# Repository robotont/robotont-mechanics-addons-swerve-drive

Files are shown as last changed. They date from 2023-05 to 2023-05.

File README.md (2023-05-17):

# Design and production files
Here are production and design files for the modular swerve drive add-on for Robotont.

The files are broken down based on file type as follows:
- step: 3D models as generally used step format;
- stl: 3D models formated for 3D printing;
- 3mf: Prusa Slicer project files containing models for 3D printing;
- gcode: files which contain gcode commands for Prusa 3D printer. (Some of the .gcode files are compressed as .zip due to github file size limitations)
- sldasm and sldprt: files containing the original 3D models designed in Solidworks.

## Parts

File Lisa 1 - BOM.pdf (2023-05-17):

## Lisa 1 – Materjalide nimekiri ühe mooduli kohta

Nr | Komponendi kirjeldus | Failinimi | Kogus | Tellimisviit | Kas prinditav/ tellitav/ freesitav
1 | Pololu 19:1 mootor 37Dx68L mm 12V koos 64 CPR kodeerijaga | BDSG-37-40-R150_motor [38] | 2 | https://www.pololu.com/product/4751/spe cs (https://www.pololu.com/product/4751/specs) | tellitav
2 | Rulluisuratas

70x25mm

scooter_wheel_7

0mm

1 | https://www.pololu.c

om/product/3272 (https://www.pololu.com/product/3272)

kasutatud

prototüübis:

https://kaup24.ee/et/s

port-puhkus-

turism/jalgrattad-

rulluisud-

rulad/rulluisud/rullui

surattad-nils-

extreme-70x24-mm-

82a-

mustad?id=5890108

&mid=7538983&ut

m_campaign=17169

_EE&utm_content=c

art_block&utm_med

ium=email&utm_so

urce=transactional&

utm_subscriber=119

580977 (https://kaup24.ee/et/sport-puhkus-turism/jalgrattad-rulluisud-rulad/rulluisud/rulluisurattad-nils-extreme-70x24-mm-82a-mustad?id=5890108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)

tellitav

3 | Ratta kinnitus võllile (võlli diameeter 6mm) | wheel_mount_h ub2 | 1 | https://www.pololu.com/product/2674 (https://www.pololu.com/product/2674) (komplekt) | tellitav/ prinditav
4 | Ratta kinnituse vastus | wheel_mount_h ub1 | 1 | | tellitav/ prinditav
5 | ratta võll l=59.1mm tihke istuga | shaft_round_wc ut_6mm_for_wh eel | 1 | https://www.alas-kuul.ee/lineaarjuhik-karastatud-ja-lihvitud-59-hrc-iso-h6-ots-markeeritud-rohelise-varviga-ljm-6-mad-1000-mm (https://www.alas-kuul.ee/lineaarjuhik-karastatud-ja-lihvitud-59-hrc-iso-h6-ots-markeeritud-rohelise-varviga-ljm-6-mad-1000-mm) | tellitav
6 | vedava mootori ülekande võll l=16.7mm tihke istuga | shaft_round_wc ut_6mm_for_mo tor_transmission 1 | 1 | https://www.alas-kuul.ee/lineaarjuhik-karastatud-ja-lihvitud-59-hrc-iso-h6-ots-markeeritud-rohelise-varviga-ljm-6-mad-1000-mm (https://www.alas-kuul.ee/lineaarjuhik-karastatud-ja-lihvitud-59-hrc-iso-h6-ots-markeeritud-rohelise-varviga-ljm-6-mad-1000-mm) | tellitav
7 | keskmiste hammasrataste ülekande võll l=45.1mm | shaft_round_wc ut_6mm_for_mi dgears | 1 | https://www.alas-kuul.ee/lineaarjuhik-karastatud-ja-lihvitud-59-hrc-iso-h6-ots-markeeritud-rohelise-varviga-ljm-6-mad-1000-mm (https://www.alas-kuul.ee/lineaarjuhik-karastatud-ja-lihvitud-59-hrc-iso-h6-ots-markeeritud-rohelise-varviga-ljm-6-mad-1000-mm) | tellitav
8 | võll ratta kõrvale koonushammasrat aste ülekandele l=49.5mm tihke istuga | shaft_round_wc ut_6mm_for_be vel_wheel_trans mission | 1 | https://www.alas-kuul.ee/lineaarjuhik-karastatud-ja-lihvitud-59-hrc-iso-h6-ots-markeeritud- (https://www.alas-kuul.ee/lineaarjuhik-karastatud-ja-lihvitud-59-hrc-iso-h6-ots-markeeritud-rohelise-varviga-ljm-6-mad-1000-mm) | tellitav

| | | | rohelise-varviga-ljm-6-mad-1000-mm (https://www.alas-kuul.ee/lineaarjuhik-karastatud-ja-lihvitud-59-hrc-iso-h6-ots-markeeritud-rohelise-varviga-ljm-6-mad-1000-mm)
9 | Koonushammasra tas ratta ülekandele väline 1.5M 16GT | bevel_gear_1.5 M_16GT_35570 700 | 1 | https://www.maedler.de/Article/35570700 (https://www.maedler.de/Article/35570700) | tellitav/ prinditav
10 | Koonushammasra tas ratta ülekandele sisemine 1.5M 16GT | bevel_gear_1.5 M_16GT_35570 700_inner | 1 | https://www.maedler.de/Article/35570700 (https://www.maedler.de/Article/35570700) | tellitav/ prinditav
11 | Silinderhammasra tas 72T 1M alumine | spur_gear_lower _1M_72T_2830 7201 | 1 | https://www.maedler.de/Article/28307201 (https://www.maedler.de/Article/28307201) | tellitav/ prinditav
12 | Silinderhammasra tas 72 1M ülemine | spur_gear_upper _1M_72T_2830 7201 | 1 | https://www.maedler.de/Article/28307201 (https://www.maedler.de/Article/28307201) | tellitav/ prinditav
13 | 72T-de vaheline hammasratas 26T 1M | spur_gear_long_ hub_26T_28302 601 | 1 | https://www.maedler.de/Article/28302601 (https://www.maedler.de/Article/28302601) | tellitav/ prinditav
14 | 72T-de vaheline hammasratas 26 T 1M, topelt keskmikuga, koonushammasrat ta võllil | spur_gear_26T_ mid_double_hub _28302601 | 1 | https://www.maedler.de/Article/28302601 (https://www.maedler.de/Article/28302601) | tellitav/ prinditav
15 | Koonushammasra tas 1M 16GT pöörava mootori (1.) nurkülekanne | small_bevel_gea r_1M_16GT_35 550701 | 1 | https://www.maedler.de/Article/35550701 (https://www.maedler.de/Article/35550701) | tellitav/ prinditav

16 | Koonushammasra tas 1M 16GT pöörava mootori nurkülekanne, lühem | small_bevel_gea r_CUT_1M_16 GT_35550701 | 1 | https://www.maedler.de/Article/35550701 (https://www.maedler.de/Article/35550701) | tellitav/ prinditav
17 | 26T 1M hammasratta väline ülekanne 1. mootori (pöörav) jaoks | spur_gear_CUT _26T_28302601 | 1 | https://www.maedler.de/Article/28302601 (https://www.maedler.de/Article/28302601) | tellitav/ prinditav
18 | Komponendi 16 ja 17 ühendatud versioon (alternatiivne printimiseks) | small_bevel_gea r1M_merged_wi th_spur_gear26 T_28302601_35 550701 | 1 | - | prinditav
19 | Silinderhammasra tas 24T 1M vedava mootori ülekanne | spur_gear_secon d_motor_transm ission_1M_24T _28302401 | 1 | https://www.maedler.de/Article/28302401 (https://www.maedler.de/Article/28302401) | tellitav/ prinditav
20 | Rulluisurattale 70mm kuullaager sisemine D=6mm, väline D=19mm, W=6mm | ball_bearing_SK F626 | 2 | https://tellimiskeskus.moduator.ee/index.php?pg=1&tg=155&kg=30&aid=52789 (https://tellimiskeskus.moduator.ee/index.php?pg=1&tg=155&kg=30&aid=52789) | tellitav
21 | Nõellaager sisemine D=6mm, väline 10mm, W=8mm | needle_roller_be aring 6-10-8 | 3 | https://tellimiskeskus.moduator.ee/index.php?pg=1&tg=155&kg=40&aid=67110 (https://tellimiskeskus.moduator.ee/index.php?pg=1&tg=155&kg=40&aid=67110) | tellitav
22 | Üherealine laager sisemine D=6mm, | ball_bearing_68 _iso_6-10-3 | 1 | https://tellimiskeskus.moduator.ee/index.p (https://tellimiskeskus.moduator.ee/index.php?pg=1&tg=155&kg=30&aid=79536) | tellitav

| väline D=10mm, W=3mm | | | hp?pg=1&tg=155&k g=30&aid=79536 (https://tellimiskeskus.moduator.ee/index.php?pg=1&tg=155&kg=30&aid=79536)
23 | Rattahoidja detaili plaat | body_wheel_hol der_plate | 1 | - | prinditav
24 | Rattahoidja detaili kõrv väiksem | body_wheel_hol der_ear_smaller | 1 | - | prinditav
25 | Rattahoidja detaili kõrv suurem | body_wheel_hol der_ear_bigger | 1 | - | prinditav
26 | Kere alumine plaat | bottom_base_pl ate | 1 | - | freesitav
27 | Kere ülemine plaat | upper_base_plat e | 1 | - | freesitav
28 | Vahepuks ema-ema kuuskant M3 sise kinnitus pikkus 40mm | support1_betwe en_plates [38] | 4 | https://www.tme.eu/ee/details/tff-m3x40_dr113/metallpuksid/dremec/113x40/ (https://www.tme.eu/ee/details/tff-m3x40_dr113/metallpuksid/dremec/113x40/) | tellitav
29 | Vahepuks ema-ema kuuskant M3 sise kinnitus pikkus 18mm | support2_upper_ plate [38] | 3 | https://www.tme.eu/ee/details/tff-m3x18_dr113/metallpuksid/dremec/113x18/ (https://www.tme.eu/ee/details/tff-m3x18_dr113/metallpuksid/dremec/113x18/) | tellitav
30 | M3 koonuspeaga kruvi 10mm | Bolt_m3_10mm [38] | 20 | https://ee.farnell.com/tr-fastenings/m3-10-m4a2mccsk-t10sf/screw-countersunk-hex-socket-m3/dp/2846508 (https://ee.farnell.com/tr-fastenings/m3-10-m4a2mccsk-t10sf/screw-countersunk-hex-socket-m3/dp/2846508) | tellitav
31 | M3 koonuspeaga kruvi 12mm | Bolt_m3_12mm 25] | 2 | https://ee.farnell.com/tr-fastenings/m3-12- (https://ee.farnell.com/tr-fastenings/m3-12-m4a2mc-s50-csk-t10/screw-countersunk-hex-socket-m3/dp/2846515) | tellitav

| | | | m4a2mc-s50-csk-t10/screw-countersunk-hex-socket-m3/dp/2846515 (https://ee.farnell.com/tr-fastenings/m3-12-m4a2mc-s50-csk-t10/screw-countersunk-hex-socket-m3/dp/2846515)
32 | M3 koonuspeaga kruvi 16mm | Bolt_m3_16mm 25] | 4 | https://uk.farnell.com/multicomp-pro/mp006522/screw -flat-csk-head-pozidriv-m3/dp/3666715?st= m3%20countersink %2016 (https://uk.farnell.com/multicomp-pro/mp006522/screw-flat-csk-head-pozidriv-m3/dp/3666715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) | tellitav
33 | M3 mutter kaheksakant | M3_stopper_nut 25] | 9 | https://ee.farnell.com/tr-fastenings/m3-n5st-z100/nut-locking-steel-bzp-m3-pk100/dp/1420431?st=m3%20stopper%2 0nut (https://ee.farnell.com/tr-fastenings/m3-n5st-z100/nut-locking-steel-bzp-m3-pk100/dp/1420431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) | tellitav
34 | M3 koonuspeaga kruvi 25mm | Bolt_m3_25mm 25] | 3 | https://ee.farnell.com/tr-fastenings/m325krstmcz100/pozi-csk-head-machine-screw-steel/dp/2770707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 %2025 (https://ee.farnell.com/tr-fastenings/m325krstmcz100/pozi-csk-head-machine-screw-steel/dp/2770707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) | tellitav

35 | isekeermestavad kruvid ratta kinnitamiseks M3 6mm | M3x6.0_set_scr ew[39] | 9 | https://ee.farnell.com/tr-fastenings/m3-6-hs45pc-s100/set-screw-socket-pcp-m3x6-pk100/dp/1419732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 q%206 (https://ee.farnell.com/tr-fastenings/m3-6-hs45pc-s100/set-screw-socket-pcp-m3x6-pk100/dp/1419732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) | tellitav
36 | Sisendid (ing. k inserts) M3 6mm | M3_insert_Stan dard [40] | 4 | https://www.prusa3d.com/product/threade d-inserts-m3-standard-100-pcs/ (https://www.prusa3d.com/product/threaded-inserts-m3-standard-100-pcs/) | tellitav
37 | isekeermestavad kruvid kahe puksi vahele 10mm M3 | M3x10.0_set_sc rew[39] | 2 | https://ee.farnell.com/tr-fastenings/m2-10-hs45pc-s25/set-screw-socket-pcp-m2x10-pk25/dp/1419725 (https://ee.farnell.com/tr-fastenings/m2-10-hs45pc-s25/set-screw-socket-pcp-m2x10-pk25/dp/1419725) | tellitav

Kõik hammasrattad on tellitavad, kuid siseaugu diameeter ning keskmiku mõõdud on disainis

modifitseeritud.

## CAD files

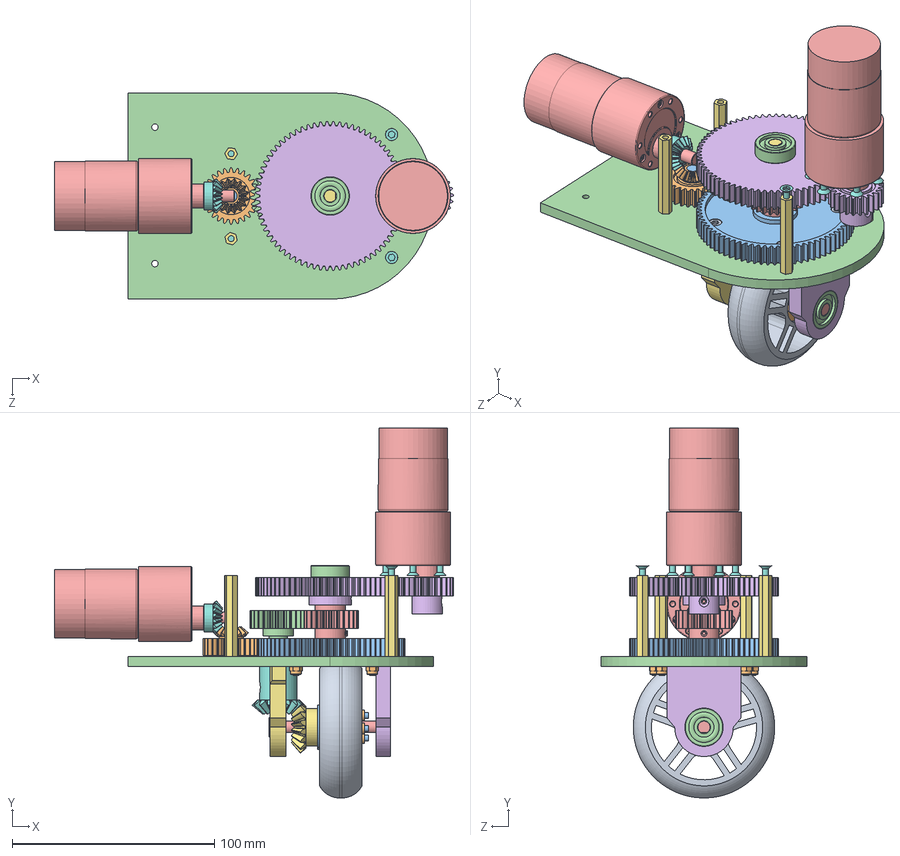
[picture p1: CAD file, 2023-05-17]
sldprt/wheel_module_assem.SLDASM
197.4 x 183.0 x 102.1 mm
scooter_wheel_70mm
wheel_mount_hub2
wheel_mount_hub1
ball_bearing_SKF626 x 2
shaft_round_wcut_6mm_for_wheel
body_wheel_holder_plate
bevel_gear_1.5M_16GT_35570700_inner
bevel_gear_1.5M_16GT_35570700
needle_roller_bearing_6-10-8 x 3
shaft_round_wcut_6mm_for_bevel_wheel_transmission
spur_gear_lower_1M_72T_28307201
spur_gear_26T_mid_double_hub_28302601
spur_gear_long_hub_26T_28302601
spur_gear_upper_1M_72T_28307201
shaft_round_wcut_6mm_for_midgears
small_bevel_gear_1M_16GT_35550701
ball_bearing_68_iso_6-10-3
small_bevel_gear1M_merged_with_spur_gear26T_28302601_35550701
shaft_round_wcut_6mm_for_motor_transmission1
bottom_base_plate
BDSG-37-40-R150_motor x 2
spur_gear_second_motor_transmission_1M_24T_28302401
support1_between_plates x 4
Bolt_m3_10mm x 16
Bolt_m3_16mm x 4
M3_stopper_nut x 7
Bolt_m3_25mm x 3
M3_insert_Standard x 4
M3x6.0 x 9
body_wheel_holder_ear_bigger
body_wheel_holder_ear_smaller

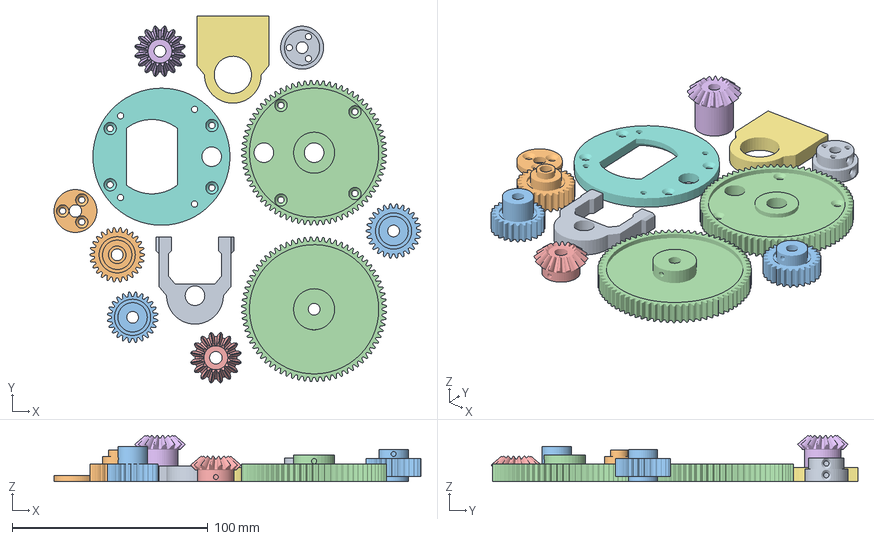
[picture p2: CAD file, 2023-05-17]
3mf/all_the_gears_and_wheel_holder.3mf
187.4 x 187.3 x 23.6 mm
v2 wheel_mount_hub1.STL
v2 wheel_mount_hub2.STL
Spur gear 1M 24T 28302401 maedler.STL
Spur gear lower 1M 72T 20PA 9FW 28307201.STL
bevel_gear_1.5M_16GT_16PT_7FW_35570700_inner.STL
bevel_gear_1.5M_16GT_16PT_7FW_35570700.STL
body_wheel_holder_ear_larger.STL
body_wheel_holder_plate.STL
body_wheel_holder_ear_bevel.STL
spur_gear_26T_mid_short_28302601.STL
spur_gear_26T_28302601.STL
Spur gear upper 1M 72T 20PA 9FW 28307201.STL

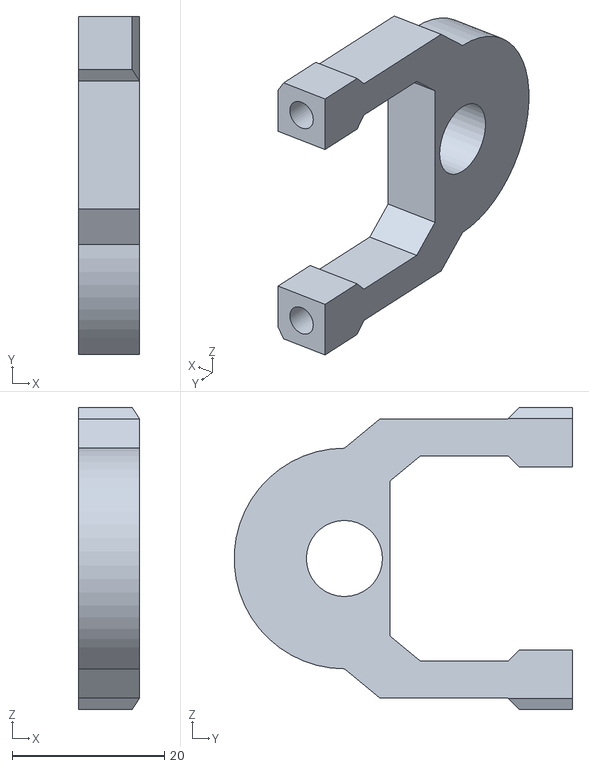
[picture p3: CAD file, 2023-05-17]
stl/body_wheel_holder_ear_bevel.STL
8.00 x 44.5 x 39.7

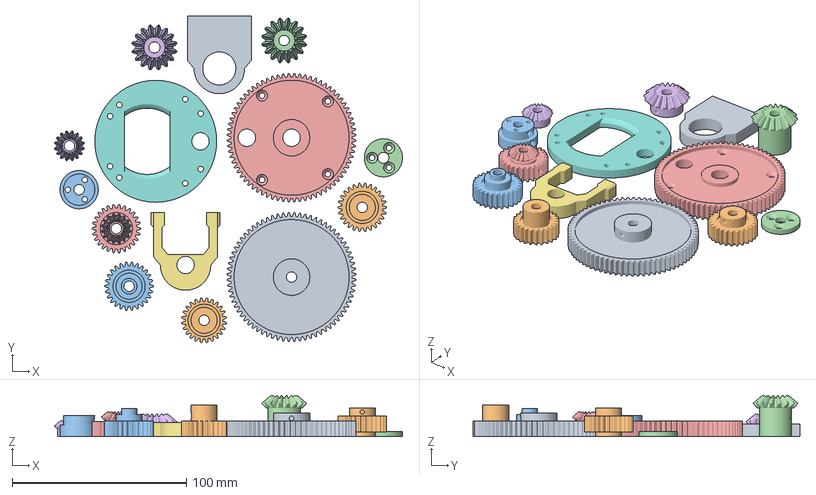
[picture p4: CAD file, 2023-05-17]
3mf/gears_Pille_PCblend.3mf
199.7 x 187.5 x 23.6 mm
Spur gear upper 1M 72T 20PA 9FW 28307201.STL
Spur gear 1M 24T 28302401 maedler.STL
v2 wheel_mount_hub1.STL
v2 wheel_mount_hub2.STL
Spur gear lower 1M 72T 20PA 9FW 28307201.STL
bevel_gear_1.5M_16GT_16PT_7FW_35570700_inner.STL
body_wheel_holder_ear_bevel.STL
body_wheel_holder_plate.STL
body_wheel_holder_ear_larger.STL
spur_gear_26T_28302601.STL
spur_gear_26T_mid_short_28302601.STL
bevel_gear_1.5M_16GT_16PT_7FW_35570700.STL
small_bevel_gear1M_merged_with_spur_gear26T_28302601_35550701.STL
small_bevel_gear_1M_16GT_35550701.STL

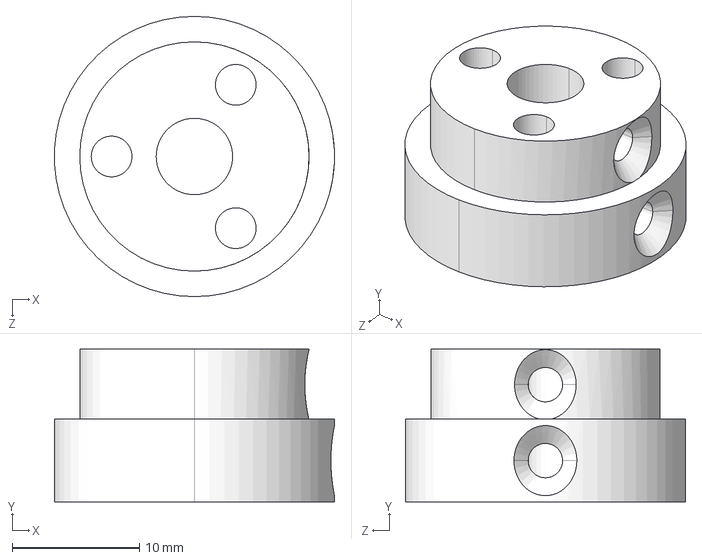
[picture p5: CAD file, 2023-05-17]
step/wheel_mount_hub1.step
22.0 x 12.0 x 22.0 mm

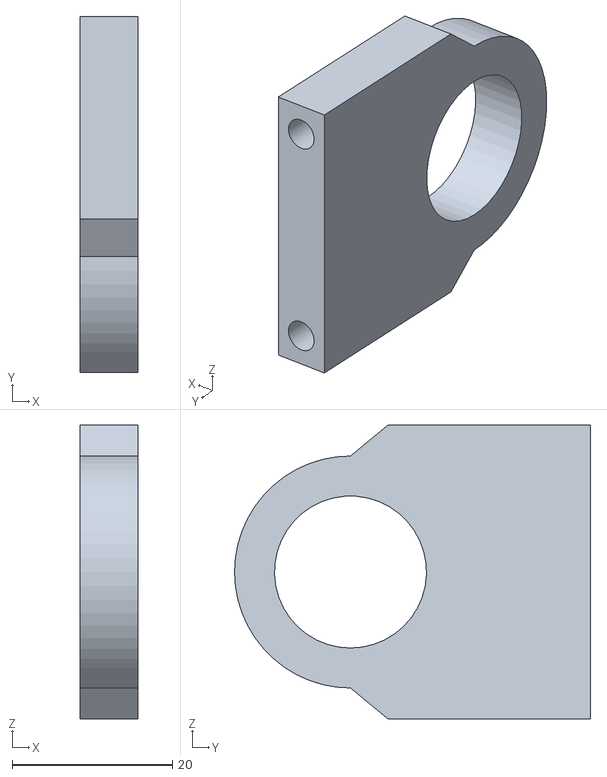
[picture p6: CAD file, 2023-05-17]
stl/body_wheel_holder_ear_larger.STL
7.20 x 44.5 x 36.7

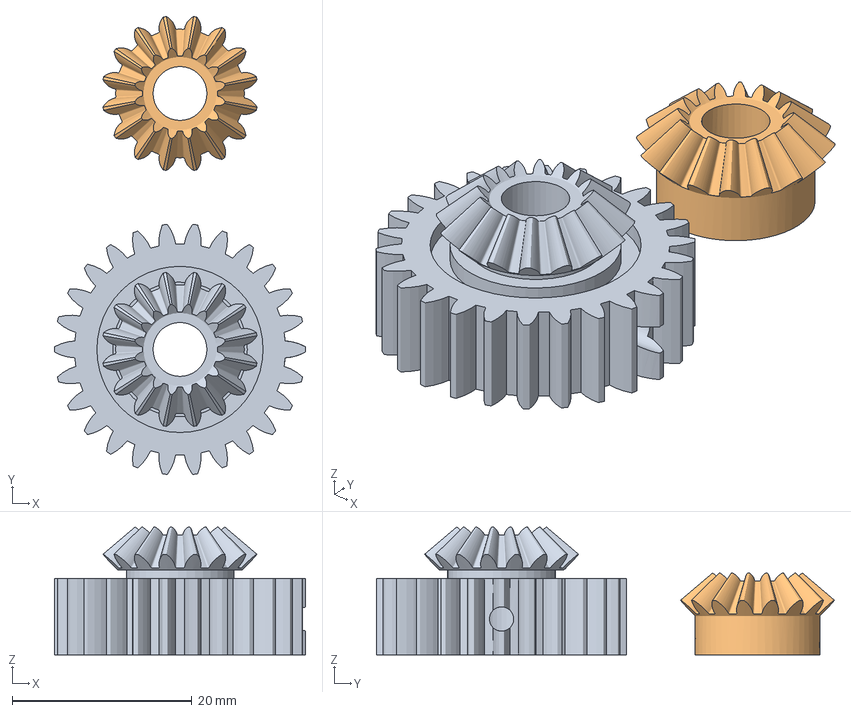
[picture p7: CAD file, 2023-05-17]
3mf/small_bevel_gears.3mf
28.0 x 51.0 x 14.2 mm
small_bevel_gear1M_merged_with_spur_gear26T_28302601_35550701.STL
small_bevel_gear_1M_16GT_35550701.STL

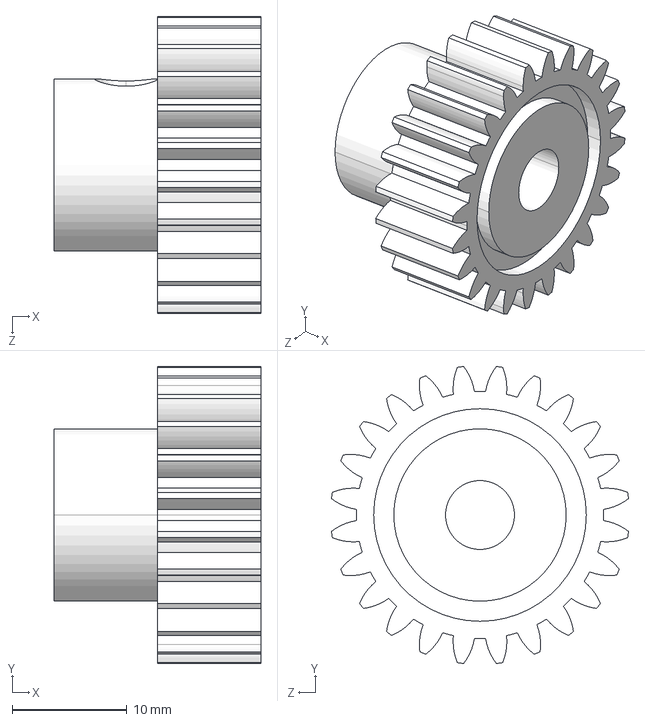
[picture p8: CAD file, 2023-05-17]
step/spur_gear_second_motor_transmission_1M_24T_28302401.step
18.0 x 25.8 x 25.8 mm

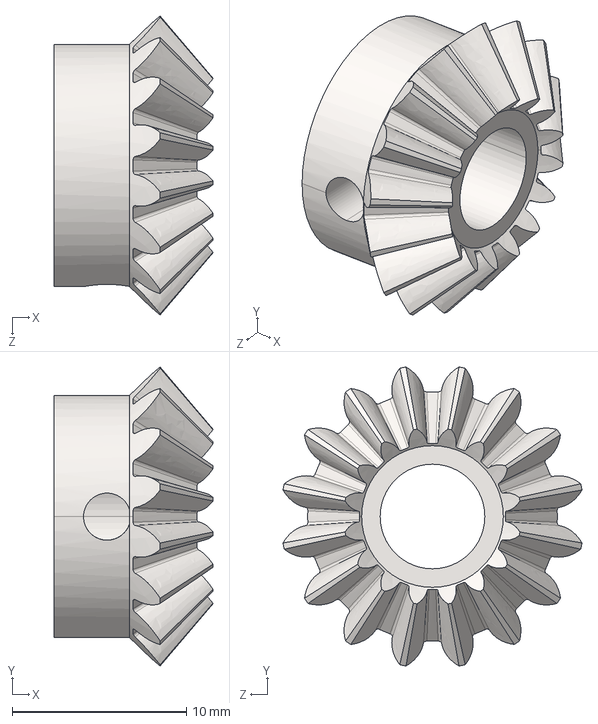
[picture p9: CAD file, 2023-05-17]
step/small_bevel_gear_1M_16GT_35550701.step
9.12 x 17.1 x 17.1 mm

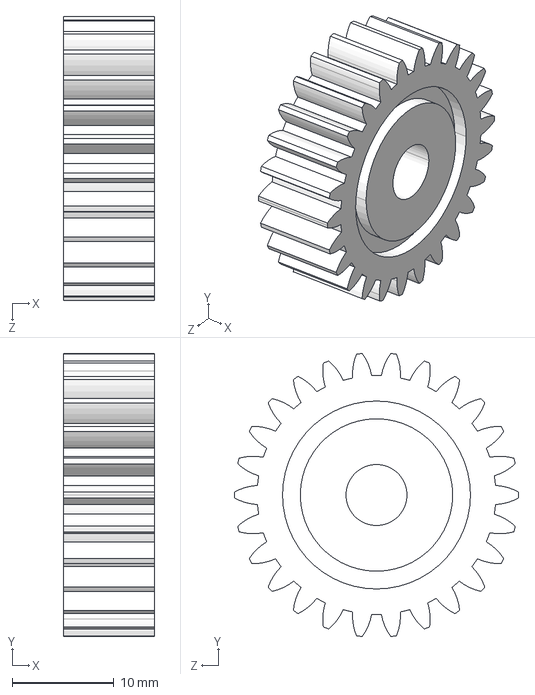
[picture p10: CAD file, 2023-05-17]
step/spur_gear_CUT_26T_28302601.step
9.00 x 27.9 x 28.0 mm

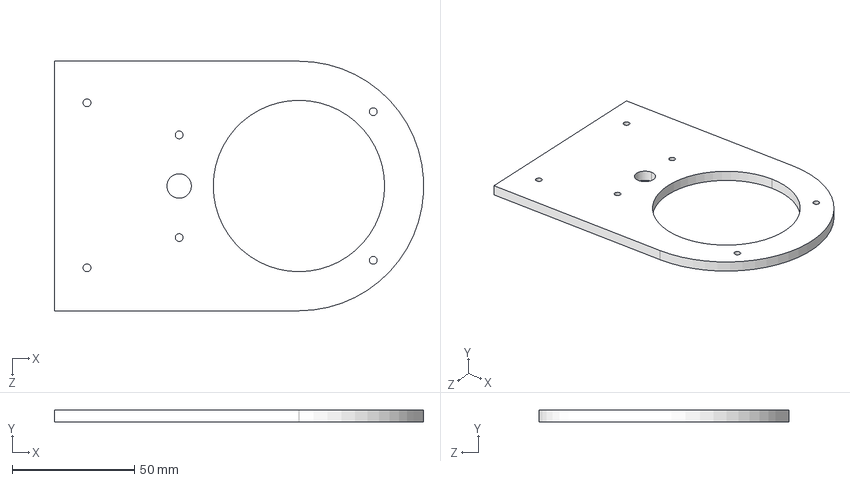
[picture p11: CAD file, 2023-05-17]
step/bottom_base_plate.step
151.0 x 5.00 x 102.1 mm

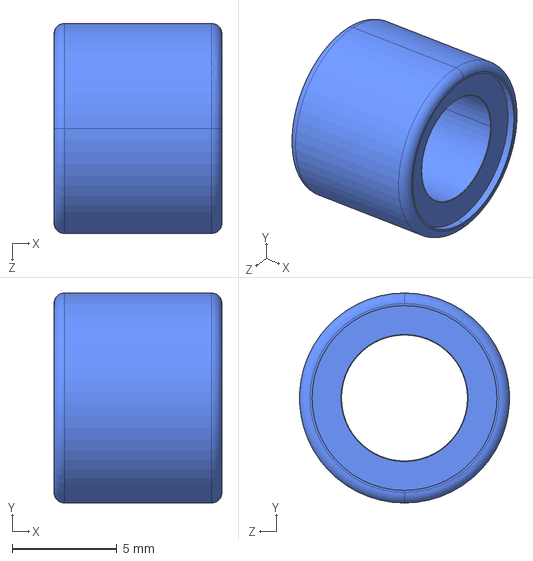
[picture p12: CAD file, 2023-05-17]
step/needle_roller_bearing_6-10-8.step
8.00 x 10.00 x 9.99 mm

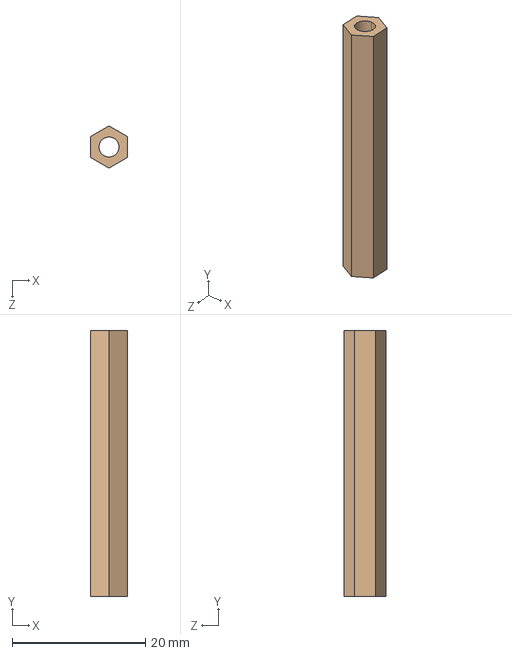
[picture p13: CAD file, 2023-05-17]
step/support1_between_plates.step
5.50 x 40.0 x 6.35 mm

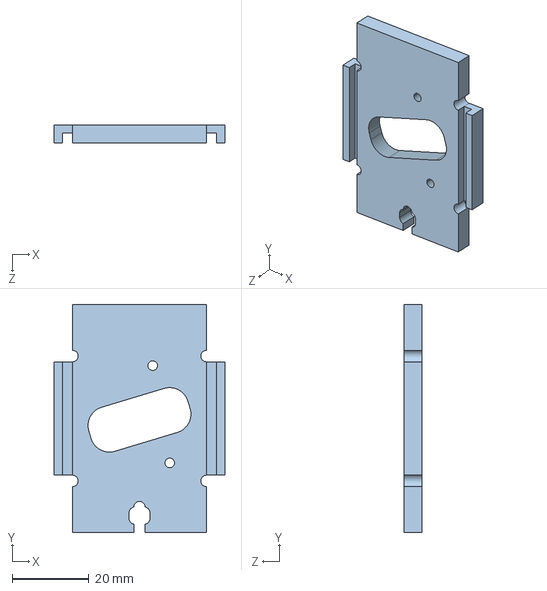
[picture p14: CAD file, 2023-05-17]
step/wheel_module_side_linear_tapp_v3.step
44.6 x 59.5 x 4.80 mm

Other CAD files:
step/scooter_wheel_70mm.step
step/spur_gear_lower_1M_72T_28307201.step
step/top_plate_v2.1.step
step/spur_gear_upper_1M_72T_28307201.step
sldprt/BDSG-37-40-R150_motor.SLDPRT
sldprt/Bolt_m3_10mm.SLDPRT
sldprt/Bolt_m3_12mm.SLDPRT
sldprt/Bolt_m3_16mm.SLDPRT
sldprt/Bolt_m3_25mm.SLDPRT
sldprt/Bottom_plate_v2.1.1.SLDPRT
sldprt/M3_insert_Standard.SLDPRT
sldprt/M3_stopper_nut.SLDPRT
sldprt/M3x10.0_set_screw.SLDPRT
sldprt/M3x6.0.SLDPRT
sldprt/ball_bearing_68_iso_6-10-3.SLDPRT
sldprt/ball_bearing_SKF626.SLDPRT
sldprt/bevel_gear_1.5M_16GT_35570700.SLDPRT
sldprt/bevel_gear_1.5M_16GT_35570700_inner.SLDPRT
sldprt/body_wheel_holder_ear_bigger.SLDPRT
sldprt/body_wheel_holder_ear_smaller.SLDPRT
sldprt/body_wheel_holder_plate.SLDPRT
sldprt/bottom_base_plate.SLDPRT
sldprt/motor_mount_back_linear_tapp_v3.SLDPRT
sldprt/motor_mount_front_linear_tapp_v3.SLDPRT
sldprt/needle_roller_bearing_6-10-8.SLDPRT
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

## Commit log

2023-05-17 Add files via upload
    Added stl files swerve drive.
    [bevel_gear_1.5M_16GT_35570700.STL, bevel_gear_1.5M_16GT_35570700_inner.STL, body_wheel_holder_ear_bevel.STL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]
2023-05-17 Add files via upload
    Uploaded swerve drive sldprt and asm files.
    [BDSG-37-40-R150_motor.SLDPRT, Bolt_m3_10mm.SLDPRT, Bolt_m3_12mm.SLDPRT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]
2023-05-17 Add files via upload
    Uploaded step files to swerve drive.
    [BDSG-37-40-R150_motor.step, Bolt_m3_10mm.step, Bolt_m3_12mm.step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]
